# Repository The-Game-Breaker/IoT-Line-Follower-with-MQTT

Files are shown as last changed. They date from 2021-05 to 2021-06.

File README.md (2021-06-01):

# IoT Project
# Hardware
## Gebruikte hardware
### Electronica
| Item | Discription | Price | Qty | Extra costs | Total |
| --- | --- | --- | --- | --- | --- |
| Cytron Maker Line | Simplifying Line Sensor for BeginnersSKU: 19064  |  11,95 € | 1 | |  11,95 €  |
| Shipping Sensor | Shipping elektor | | 1 |  7,95 € |  7,95 € |
| PCB mainboard | PCB robot driver board |  0,51 €  | 1 | |  0,51 € |
| SHIPPING CHARGE | SHIPPING | | 1 |  12,63 € |  12,63 €  |
| PAYPAL FEE | PAYPAL FEE | | 1 |  0,41 € |  0,41 € |
| DRV8825 driver | DSD00010 \_Stepstick DRV8825 drive with heatsink |  5,00 €  | 2 | |  10,00 €  |
| Inbusstelschroef M4x5 | DBM00194 \_Inbusstelschroef M4x5 (10 stuks) |  2,30 €  | 1 | |  2,30 € |
| Verzend- en administratiekosten | Verzend- en administratiekosten 123-3D.nl | | 1 |  5,95 € |  5,95 € |
| Lipo Battery | Yuki Kryptonium 3S 11.1V 30C 5000mAh LiPo 801323 |  45,99 € | 1 | |  45,99 €  |
| Step-Down Buck Converter | DEBO DCDC DOWN 4 (mini 360) |  2,02 €  | 1 | |  2,02 € |
| Dupont kit | Dupont connector kit |  5,00 €  | 1 | |  5,00 € |
| Fuse holder | fuse holder |  0,30 €  | 1 | |  0,30 € |
| Fuse | fuse 2A |  0,20 €  | 1 | |  0,20 € |
| RGB led | RGB common cathode |  1,03 €  | 2 | |  2,06 € |
| 3mm led | 3mm led red |  0,05 €  | 2 | |  0,10 € |
| Resistors | resistors various values |  0,02 €  | 8 | |  0,13 € |
| HC-SR04 | HC-SR04 Ultrasonic sensor – afstandsmeter |  3,00 €  | 1 | |  3,00 € |
| capacator | capacator |  0,11 €  | 2 | |  0,22 € |
| 3D print | 3d prints materiaal+manafacturing |  20,00 € | 1 | |  20,00 €  |
| Lasercut frame | laserkcut frame matriaal+manafacturing |  20,00 € | 1 | |  20,00 €  |
| Stepper motor | JK42HS34-1334 |  13,00 € | 2 | |  26,00 €  |
| Hardware | varous nuts and bolts |  15,00 € | 1 | |  15,00 €  |
| Knikkers | knikkers |  0,20 €  | 2 | |  0,40 € |
| | | | | |  192,12 € |
#### Cytron Maker-Line

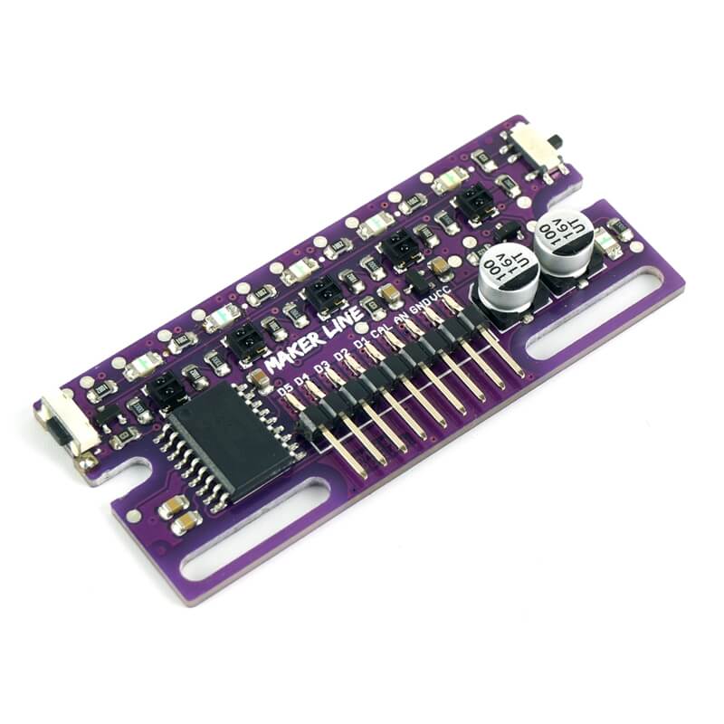
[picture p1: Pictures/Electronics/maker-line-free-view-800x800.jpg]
maker-line-free-view-800x800


De Cytron Maker-Line is een ir sensor array voorzien van 5 sensoren die de lijn uitlezen. Op basis van deze output sturen we de motoren aan. Deze module geeft ook nog wat extra &quot;creature-comforts&quot;, zo is de array gemakkelijk te kalibreren en kan deze &quot;geswitchted&quot; worden tussen een donkere of lichte lijn.

#### HC-SR04

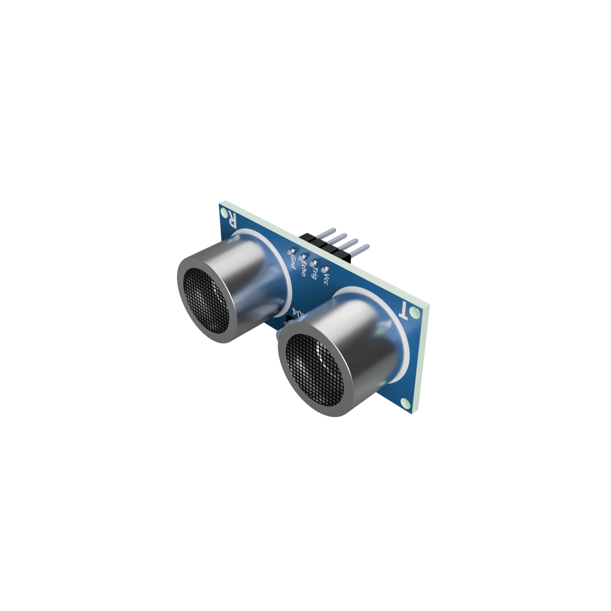
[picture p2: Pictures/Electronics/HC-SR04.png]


De HC-SR04 is een ultrasone sensor. Deze moet ervoor zorgen dat het wagentje nergens tegenaan rijdt. Dit wordt tot stand gebracht met ultrasone echolocatie.

#### Joy-IT Esp32
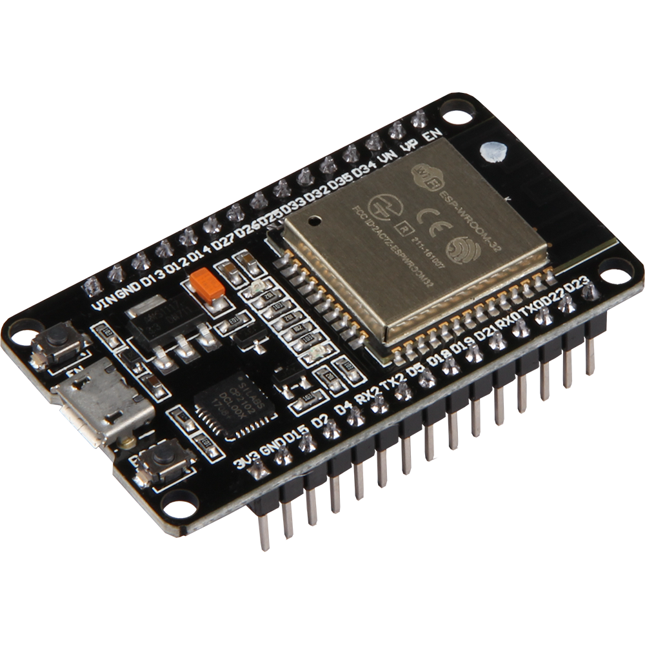
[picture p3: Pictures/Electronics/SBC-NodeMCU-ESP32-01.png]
 

Het brein van het project wordt de ESP32 van JOY-IT. Deze zal alle in- en outputs aansturen en data communiceren via wifi.

### nema17 stepper motor

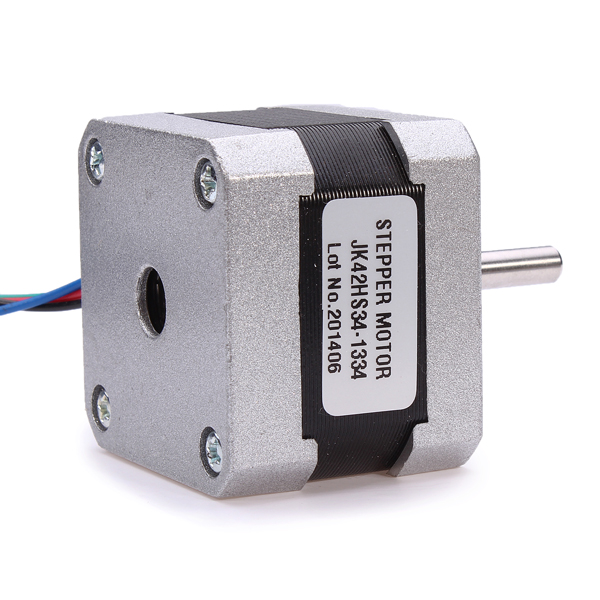
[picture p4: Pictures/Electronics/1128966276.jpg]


Deze JK42HS34-1334 NEMA 17 stepper motoren worden gebruikt om het wagentje aan te drijven. Hoewel niet de ideale keuze, bieden ze toch enige flexibiliteit ten opzichte van andere oplossingen. Een andere factor voor deze keuze was dat ik deze nog had liggen en ik er graag eens mee wilde werken.

#### DRV8825 stepper motor driver

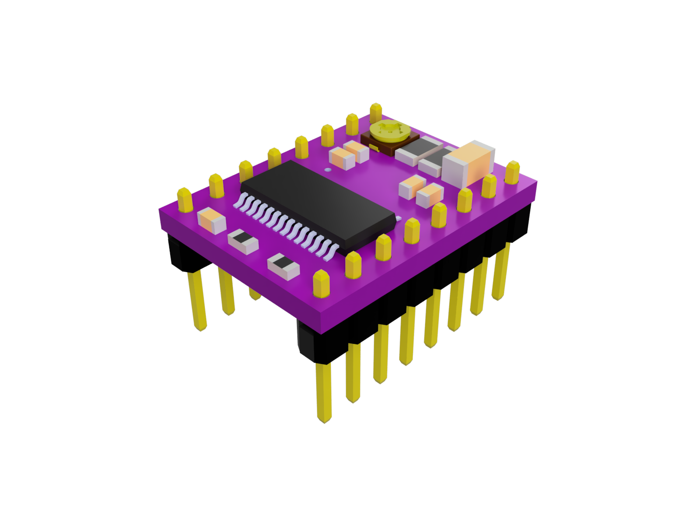
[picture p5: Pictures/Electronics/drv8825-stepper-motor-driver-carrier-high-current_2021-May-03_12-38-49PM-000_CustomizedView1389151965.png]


De DRV8825 wordt gebruikt om de NEMA 17 motoren aan te sturen. Niet alleen biedt deze driver een hogere ampère levering, de microsteps kunnen ook makkelijk worden ingesteld

#### RGB LED 5mm

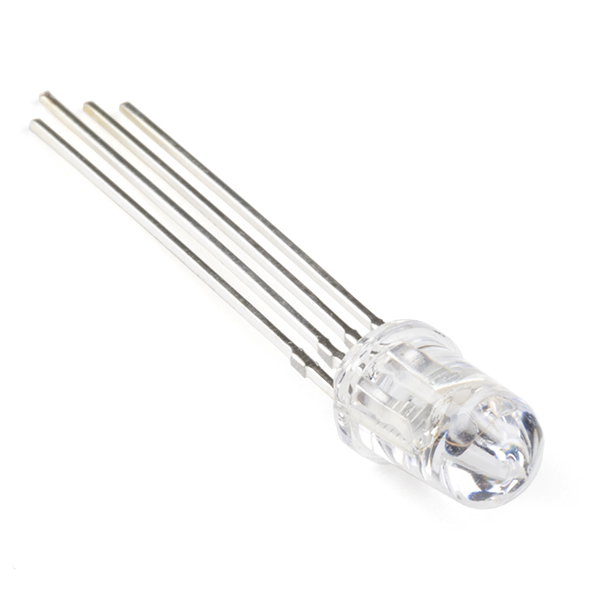
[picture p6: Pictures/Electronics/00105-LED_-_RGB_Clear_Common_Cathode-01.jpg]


Deze led wordt gebruikt als indicator voor de status van het wagentje.

Deze statussen zijn:

- Rood: Het wagentje is de lijn kwijt
- Groen: Het wagentje volgt de lijn en geeft aan naar welke kant er wordt gedraaid
- Blauw: Het wagentje stopt voor een obstakel. Dit kan een blokkade of een dwarslijn zijn.

### Schema, PCB
####

Het onderstaand schema geeft de beschreven componenten systematisch weer.

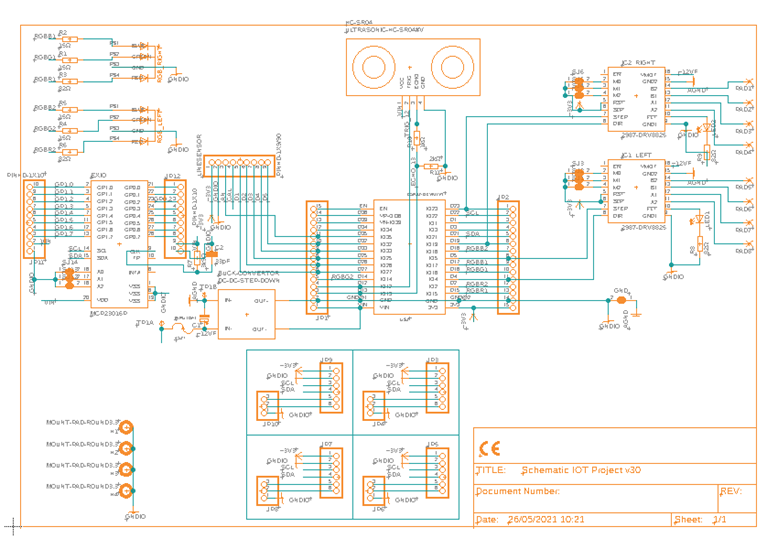
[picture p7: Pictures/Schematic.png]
 
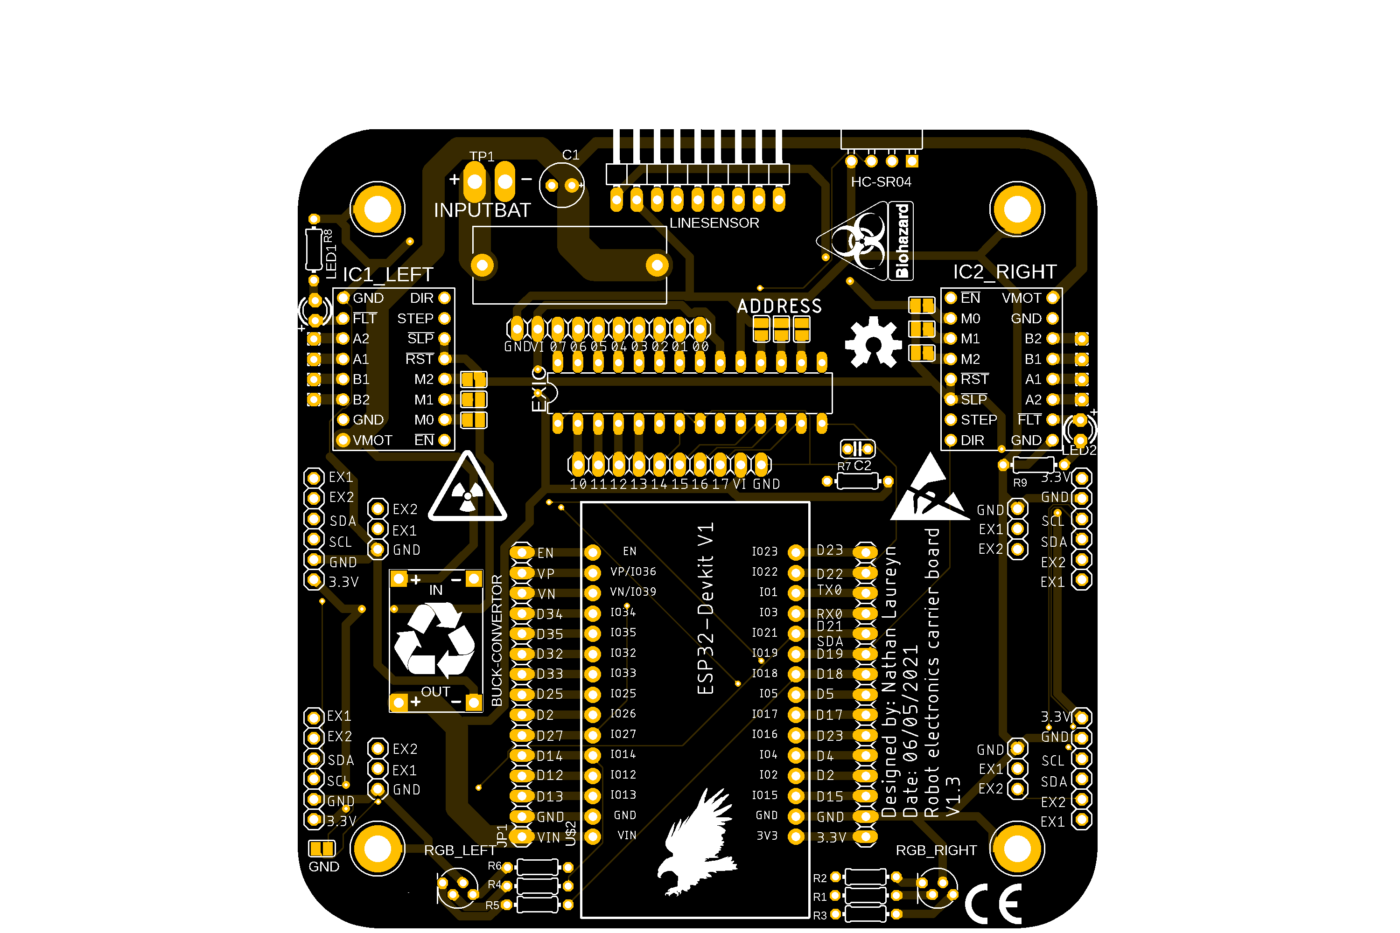
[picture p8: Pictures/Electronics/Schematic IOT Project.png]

### Hardware, andere componenten
#### Chassis



Het chassis bestaat uit een eigen ontwerp vervaardigd uit plexiglas en 3D-geprinte (r)PETG-onderdelen. Deze zijn aan elkaar verbonden met M3, M4 en M5 bouten en moeren uit RVS.
#### Wielen

Er zijn 2 wielen voorzien die instaan voor de aandrijving en sturing van het wagentje. Deze komen oorspronkelijk van een RC-auto. Ook zijn er 2 kogelwieltjes voorzien om het wagentje stabiel te houden.
# Code
## Overview
Programmatie werd geschreven in Visual Studio Code met platformio. Dit geeft een aantal voordelen qua debuggen en foutcontrole maar brengt ook een aantal challenges met zich mee. De code wordt opgedeeld in verschillende onderdelen.

### Setup: includes, definities, integers, etc.

Eerst vinden we een sectie met declaraties en setup voor de verschillende onderdelen van het wagentje. Ook vinden we enkele &quot;macro&#39;s&quot;; deze worden gebruikt om de code en functies later leesbaarder te houden.

### Functies
Vervolgens vinden we een sectie waarin de functies zijn geschreven. Deze worden later opgevraagd door de verschillende taken of andere functies.

### Taken

Onder de functies vinden we een sectie met &quot;Tasks&quot;. Hier worden de functies gedeclareerd die later door de ESP&#39;s FreeRTOS zullen worden opgevraagd.

### Setup en Loop

Tot slot vinden we de sectie setup, hier worden de pinnen gedeclareerd en geïnitialiseerd, ook de taken worden hier toegevoegd. De loop-functie wordt in praktijk niet gebruikt in dit geval.

## FreeRTOS

In de programmatie ben ik voor een systeem gegaan met FreeRTOS in plaats van een meer traditioneel systeem. Ik heb hiervoor gekozen omdat dit het gemakkelijk en efficiënt maakt om te multitasken. Het zorgt er ook voor dat in de toekomst uitbreidingen makkelijk mogelijk zijn.

FreeRTOS werkt een beetje als een scheduler, enkel is deze ingebouwd in de ESP en vraagt dus geen extra libraries. Tevens biedt de RTOS ook een uitgebreid pakket aan opties. Zo kan je bijvoorbeeld een bepaalde taak aan een bepaalde &quot;core&quot; toewijzen en zo &quot;echte&quot; synchrone taken uitvoeren.

## Case system

| Case nr. | Sensors | L | ML | M | MR | R | Dist |
| --- | --- | --- | --- | --- | --- | --- | --- |
| 1 | ExtremeLeft | ON | OFF | OFF | OFF | OFF | OFF |
| 2 | HardLeft | ON | ON | OFF | OFF | OFF | OFF |
| 3 | MediumLeft | OFF | ON | OFF | OFF | OFF | OFF |
| 4 | SoftLeft | OFF | ON | ON | OFF | OFF | OFF |
| 5 | Strait | OFF | OFF | ON | OFF | OFF | OFF |
| 6 | SoftRight | OFF | OFF | ON | ON | OFF | OFF |
| 7 | MediumRight | OFF | OFF | OFF | ON | OFF | OFF |
| 8 | HardRight | OFF | OFF | OFF | ON | ON | OFF |
| 9 | ExtremeRight | OFF | OFF | OFF | OFF | ON | OFF |
| 10 | CrossLine | ON | ON | ON | ON | ON | OFF |
| 11 | LOSTLine | OFF | OFF | OFF | OFF | OFF | OFF |
| 12 | Objectdetect | OFF | OFF | OFF | OFF | OFF | ON |

In de programmatie test de microcontroller de sensorwaarde voor verschillende cases. Aan de hand van deze waarde wordt er een &quot;casenummer&quot; gegeven. Deze kan dan worden opgevraagd door een andere taak, in dit geval de motor sturing taak (taskstep).
![](RackMultipart20210601-4-1wbuym5_html_b8db10d83fbda782.png
## Wifi en MQTT

De ESP is voorzien van een &quot;library&quot; waarmee hij via wifi met een mqtt server kan verbinden. Deze kan zowel &quot;subscriben&quot; als &quot;publishen&quot;. Zo kan hij communiceren met de node red server.
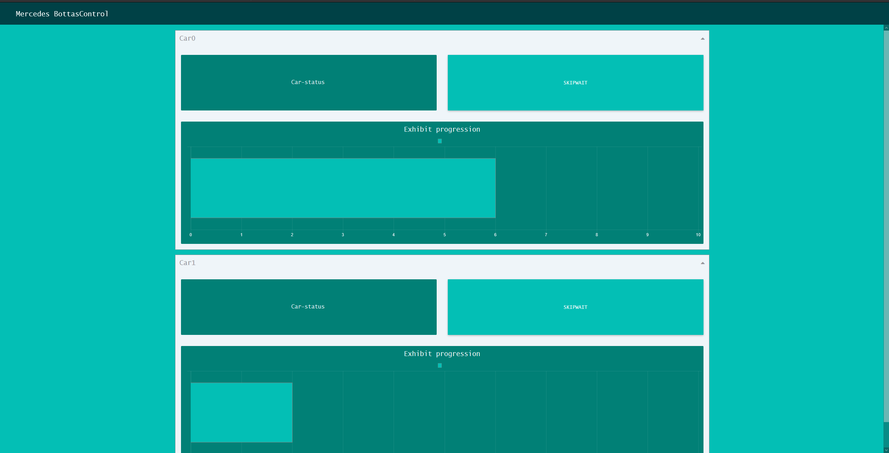
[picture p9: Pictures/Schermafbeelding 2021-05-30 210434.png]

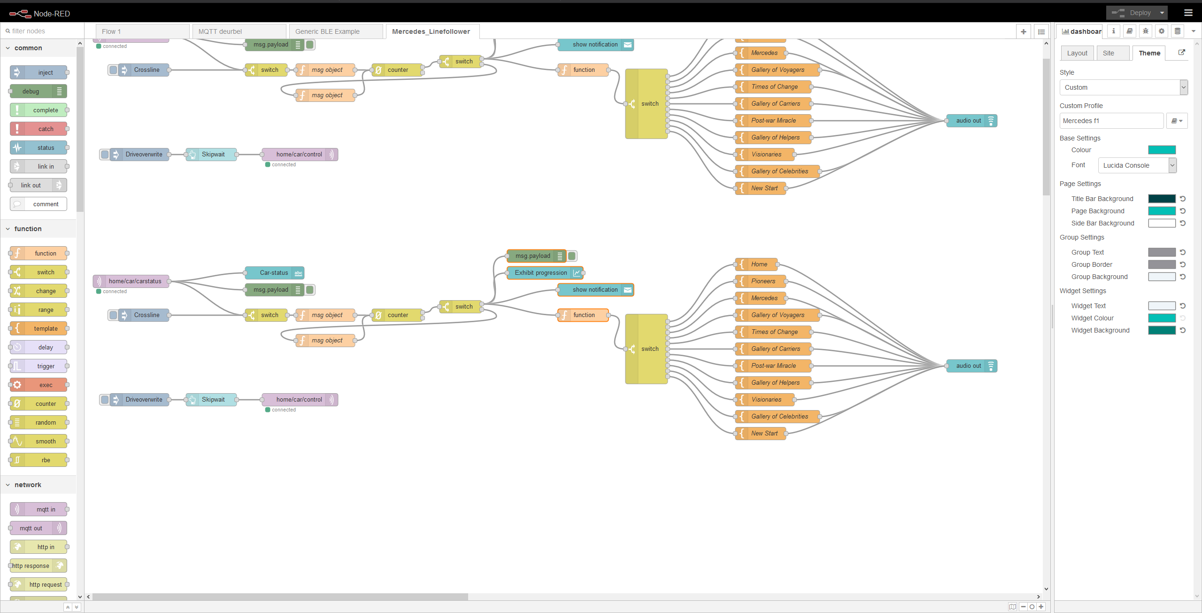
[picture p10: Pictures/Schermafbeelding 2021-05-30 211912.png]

# Tutorial

## Prerequisites

Tijdens de tutorial wordt ervan uitgegaan dat er kennis is van volgende elementen:

- Elektronica
- Mechanica
- ESP32 en software
- MQTT
- Node Red
- Netwerken

## Stap 1: Acquiring hardware

De eerste stap om het wagentje te bouwen is natuurlijk alle hardware en elektronica aan te kopen. Deze onderdelen werden eerder in dit document beschreven onder het deel hardware en zijn ook terug te vinden in de BOM.

## Stap 2: Assemblage

Nadat alle onderdelen zijn aangekomen, kunnen we beginnen met de assemblage van de wagentjes.

### Bodem frame

Bevestig de motor houders, zwenkwieltjes en batterijhouder aan het bodem frame met de bijhorende bouten, moeren en rondellen.

### Midden frame

Bevestig de stapper motoren in de motorhouders. Installeer de &quot;support poles&quot; op de bodemplaat. Installeer ook de bumper met line sensor.

### Boven frame

Installeer het boven frame op de &quot;support poles&quot; en bevestig deze. Installeer vervolgens de mounting bracket voor de afstandssenor.

### PCB

Soldeer alle componenten op de PCB behalve de motorkabels.

### Elektronica bevestigen

Bevestig de servo op het mounting bracket. Neem de afstand sensor en installeer deze op het bovendeel van het mounting bracket en installeer het geheel vervolgens op de servomotor. Bevestig vervolgens de pcb met de bijhorende bouten, moeren en &quot;standoffs&quot; op het boven frame.

### Afmontage Elektronica

Tot slot worden alle kabels getrokken en verbonden met de bijhorende onderdelen volgens onderstaand schema.



## Stap 3: MQTT and node red

Installeer een MQTT en Node Red server. Hierbij kan gebruik gemaakt worden van een raspberry pi.

Installeer de node-red flow voor de wagensturing.

## Stap 4: Programmatie ESP32

Nu we een MQTT-server hebben, moeten we de ESP32 programmeren. Vergeet niet voor het programmeren de code aan te passen aan de huidige situatie (wifi ssid, password, etc.). Programmeer vervolgens ESP.

## Stap 5 Aanleggen van het parcours

Het aanleggen van het parcours kan simpelweg worden gedaan door het trekken van een zwarte lijn op lichte grond of witte lijn op donkere grond. Vervolgens kunnen er dwarslijnen voorzien worden om het wagentje te stoppen op de &quot;points of intrest&quot;.

## Stap 6 Tewerkstelling

Tot slot kunnen de wagentjes in werking worden gesteld. Door deze op de lijn te plaatsen en de batterij in te steken.

# Resources

[https://grabcad.com/library/esp-wroom-32-2](https://grabcad.com/library/esp-wroom-32-2)

[https://www.cytron.io/p-maker-line-simplifying-line-sensor-for-beginner](https://www.cytron.io/p-maker-line-simplifying-line-sensor-for-beginner)

[https://www.jkongmotor.com/product/42HS-NEMA17-2Phase-Stepper-Motor-1-8%C2%B0.html](https://www.jkongmotor.com/product/42HS-NEMA17-2Phase-Stepper-Motor-1-8%C2%B0.html)

[https://www.thingiverse.com/thing:4275668/files](https://www.thingiverse.com/thing:4275668/files)

[https://www.makerguides.com/wp-content/uploads/2019/02/DRV8825-Arduino-stepper-motor-wiring-schematic-diagram-pinout\_bb-1024x551.jpg](https://www.makerguides.com/wp-content/uploads/2019/02/DRV8825-Arduino-stepper-motor-wiring-schematic-diagram-pinout_bb-1024x551.jpg)

[https://www.makerguides.com/drv8825-stepper-motor-driver-arduino-tutorial/](https://www.makerguides.com/drv8825-stepper-motor-driver-arduino-tutorial/)

[https://github.com/suzakulab/Eagle-Library-Pololu](https://github.com/suzakulab/Eagle-Library-Pololu)

[https://www.diymodules.org/eagle-show-object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](https://www.diymodules.org/eagle-show-object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)

[https://www.airspayce.com/mikem/arduino/AccelStepper/index.html](https://www.airspayce.com/mikem/arduino/AccelStepper/index.html)

[https://www.microchip.com/wwwproducts/en/MCP23016](https://www.microchip.com/wwwproducts/en/MCP23016)

[https://www.instructables.com/IO-Expander-for-ESP32-ESP8266-and-Arduino/](https://www.instructables.com/IO-Expander-for-ESP32-ESP8266-and-Arduino/)

[https://github.com/arkhipenko/TaskScheduler](https://github.com/arkhipenko/TaskScheduler)

[https://ozh.github.io/ascii-tables/](https://ozh.github.io/ascii-tables/)

[https://www.studiopieters.nl/esp32-pinout/](https://www.studiopieters.nl/esp32-pinout/)

[https://flows.nodered.org/node/node-red-dashboard](https://flows.nodered.org/node/node-red-dashboard)

## Colors:

 #004146 RGB (0,65,70)
 
 #018076 RGB (1,128,118)
 
 #03BFB5 RGB (3,191,181)
 
 #949398 RGB (148,147,152)
 
 #EFF5F9 RGB (239,245,249)

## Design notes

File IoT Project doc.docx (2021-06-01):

1/06/2021

Nathan Laureyn

# IoT Project

# Artikel I. Hardware

## Sectie I.1 Gebruikte hardware

### (a) Electronica

#### (i) Cytron Maker-Line


De Cytron Maker-Line is een ir sensor array voorzien van 5 sensoren die de lijn uitlezen. Op basis van deze output sturen we de motoren aan. Deze module geeft ook nog wat extra “creature-comforts”, zo is de array gemakkelijk te kalibreren en kan deze “geswitchted” worden tussen een donkere of lichte lijn.

#### (ii) HC-SR04

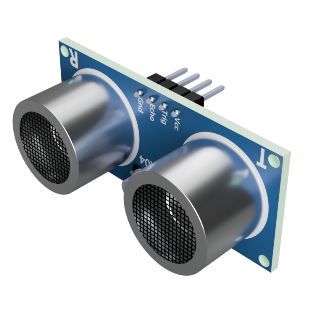
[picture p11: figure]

De HC-SR04 is een ultrasone sensor. Deze moet ervoor zorgen dat het wagentje nergens tegenaan rijdt. Dit wordt tot stand gebracht met ultrasone echolocatie.

#### (iii) Joy-IT Esp32

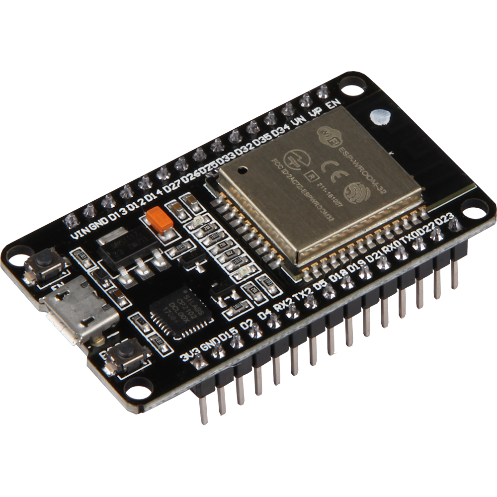
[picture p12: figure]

Het brein van het project wordt de ESP32 van JOY-IT. Deze zal alle in- en outputs aansturen en data communiceren via wifi.

### (b) nema17 stepper motor

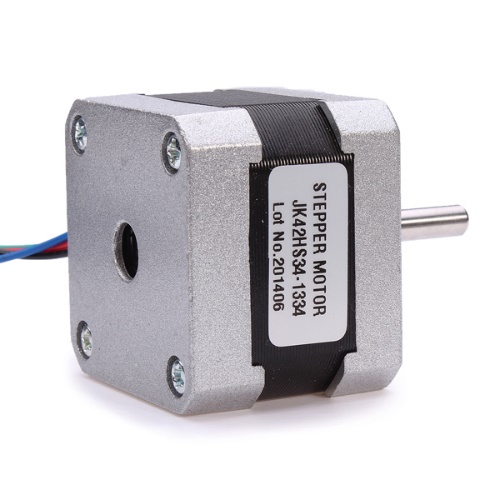
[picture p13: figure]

Deze JK42HS34-1334 NEMA 17 stepper motoren worden gebruikt om het wagentje aan te drijven. Hoewel niet de ideale keuze, bieden ze toch enige flexibiliteit ten opzichte van andere oplossingen. Een andere factor voor deze keuze was dat ik deze nog had liggen en ik er graag eens mee wilde werken.

#### (i) DRV8825 stepper motor driver

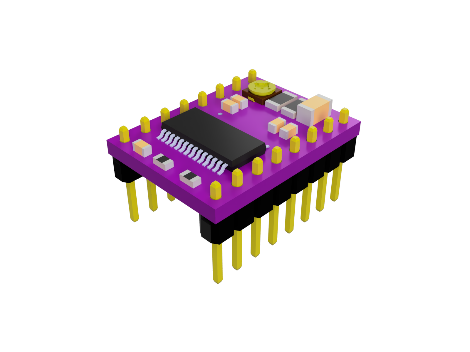
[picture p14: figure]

De DRV8825 wordt gebruikt om de NEMA 17 motoren aan te sturen. Niet alleen biedt deze driver een hogere ampère levering, de microsteps kunnen ook makkelijk worden ingesteld

#### (iii) RGB LED 5mm

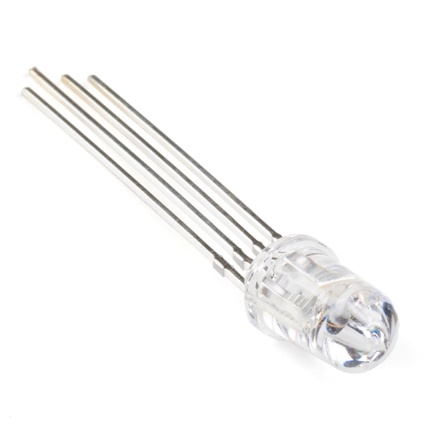
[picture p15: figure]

Deze led wordt gebruikt als indicator voor de status van het wagentje.

Deze statussen zijn:

- Rood: Het wagentje is de lijn kwijt
- Groen: Het wagentje volgt de lijn en geeft aan naar welke kant er wordt gedraaid
- Blauw: Het wagentje stopt voor een obstakel. Dit kan een blokkade of een dwarslijn zijn.

### (c) Schema, PCB

Het onderstaand schema geeft de beschreven componenten systematisch weer.

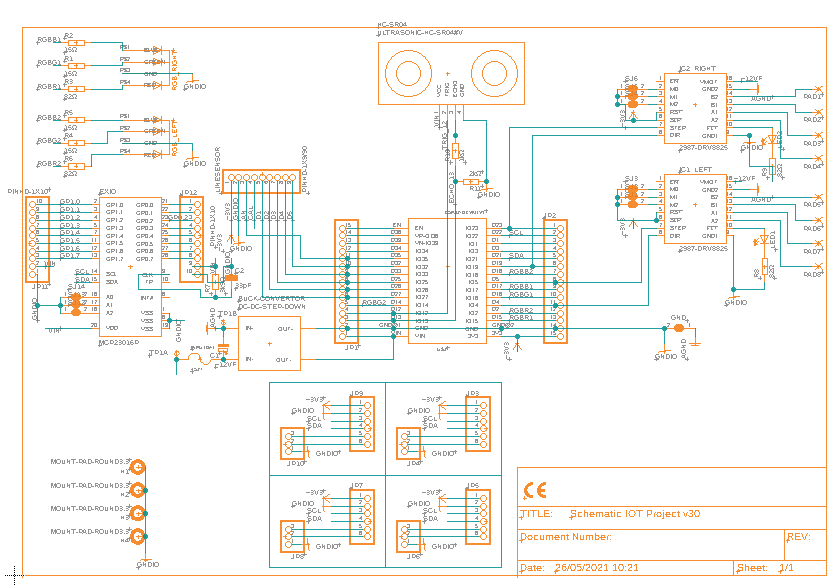
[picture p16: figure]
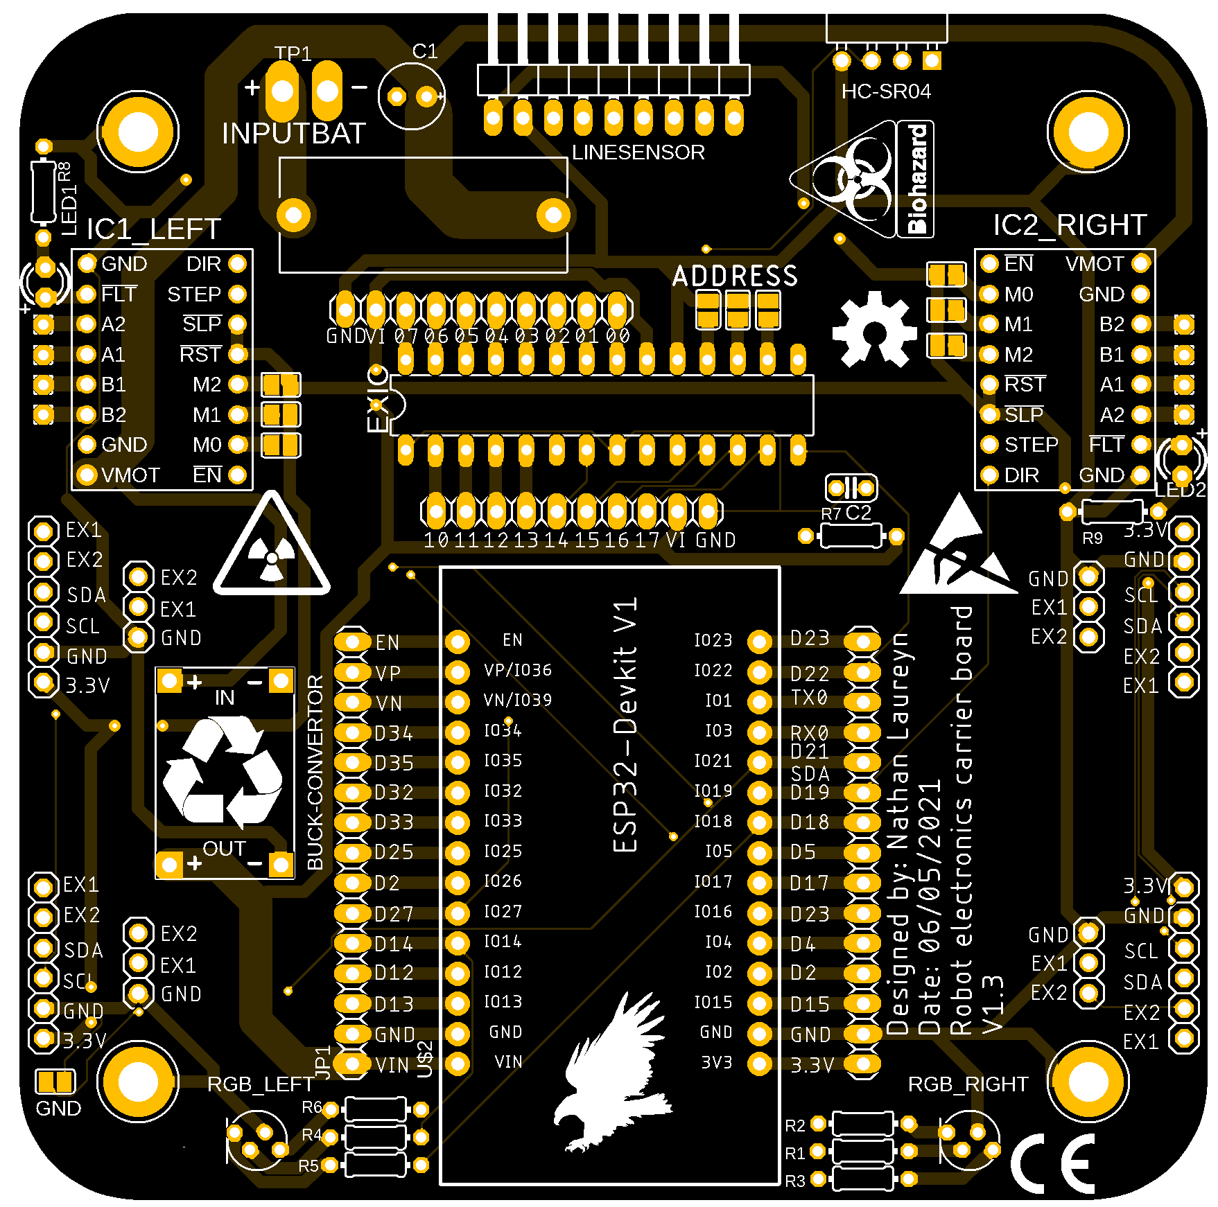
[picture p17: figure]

### (d) Hardware, andere componenten

#### (i) Chassis

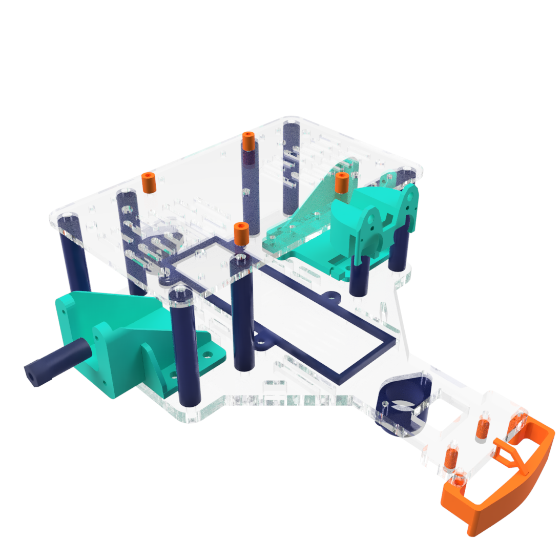
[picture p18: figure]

Het chassis bestaat uit een eigen ontwerp vervaardigd uit plexiglas en 3D-geprinte (r)PETG-onderdelen. Deze zijn aan elkaar verbonden met M3, M4 en M5 bouten en moeren uit RVS.

#### (ii) Wielen

Er zijn 2 wielen voorzien die instaan voor de aandrijving en sturing van het wagentje. Deze komen oorspronkelijk van een RC-auto. Ook zijn er 2 kogelwieltjes voorzien om het wagentje stabiel te houden.

# Artikel II. Code

## Sectie II.1 Overview

Programmatie werd geschreven in Visual Studio Code met platformio. Dit geeft een aantal voordelen qua debuggen en foutcontrole maar brengt ook een aantal challenges met zich mee. De code wordt opgedeeld in verschillende onderdelen.

### (a) Setup: includes, definities, integers, etc.

Eerst vinden we een sectie met declaraties en setup voor de verschillende onderdelen van het wagentje. Ook vinden we enkele “macro’s”; deze worden gebruikt om de code en functies later leesbaarder te houden.

### (b) Functies

Vervolgens vinden we een sectie waarin de functies zijn geschreven. Deze worden later opgevraagd door de verschillende taken of andere functies.

### (c) Taken

Onder de functies vinden we een sectie met “Tasks”. Hier worden de functies gedeclareerd die later door de ESP’s FreeRTOS zullen worden opgevraagd.

### (d) Setup en Loop

Tot slot vinden we de sectie setup, hier worden de pinnen gedeclareerd en geïnitialiseerd, ook de taken worden hier toegevoegd. De loop-functie wordt in praktijk niet gebruikt in dit geval.

## Sectie II.2 FreeRTOS

In de programmatie ben ik voor een systeem gegaan met FreeRTOS in plaats van een meer traditioneel systeem. Ik heb hiervoor gekozen omdat dit het gemakkelijk en efficiënt maakt om te multitasken. Het zorgt er ook voor dat in de toekomst uitbreidingen makkelijk mogelijk zijn.

FreeRTOS werkt een beetje als een scheduler, enkel is deze ingebouwd in de ESP en vraagt dus geen extra libraries. Tevens biedt de RTOS ook een uitgebreid pakket aan opties. Zo kan je bijvoorbeeld een bepaalde taak aan een bepaalde “core” toewijzen en zo “echte” synchrone taken uitvoeren.

## Sectie II.3 Case system

Case nr. | Sensors | L | ML | M | MR | R | Dist
1 | ExtremeLeft | ON | OFF | OFF | OFF | OFF | OFF
2 | HardLeft | ON | ON | OFF | OFF | OFF | OFF
3 | MediumLeft | OFF | ON | OFF | OFF | OFF | OFF
4 | SoftLeft | OFF | ON | ON | OFF | OFF | OFF
5 | Strait | OFF | OFF | ON | OFF | OFF | OFF
6 | SoftRight | OFF | OFF | ON | ON | OFF | OFF
7 | MediumRight | OFF | OFF | OFF | ON | OFF | OFF
8 | HardRight | OFF | OFF | OFF | ON | ON | OFF
9 | ExtremeRight | OFF | OFF | OFF | OFF | ON | OFF
10 | CrossLine | ON | ON | ON | ON | ON | OFF
11 | LOSTLine | OFF | OFF | OFF | OFF | OFF | OFF
12 | Objectdetect | OFF | OFF | OFF | OFF | OFF | ON

In de programmatie test de microcontroller de sensorwaarde voor verschillende cases. Aan de hand van deze waarde wordt er een “casenummer” gegeven. Deze kan dan worden opgevraagd door een andere taak, in dit geval de motor sturing taak (taskstep).

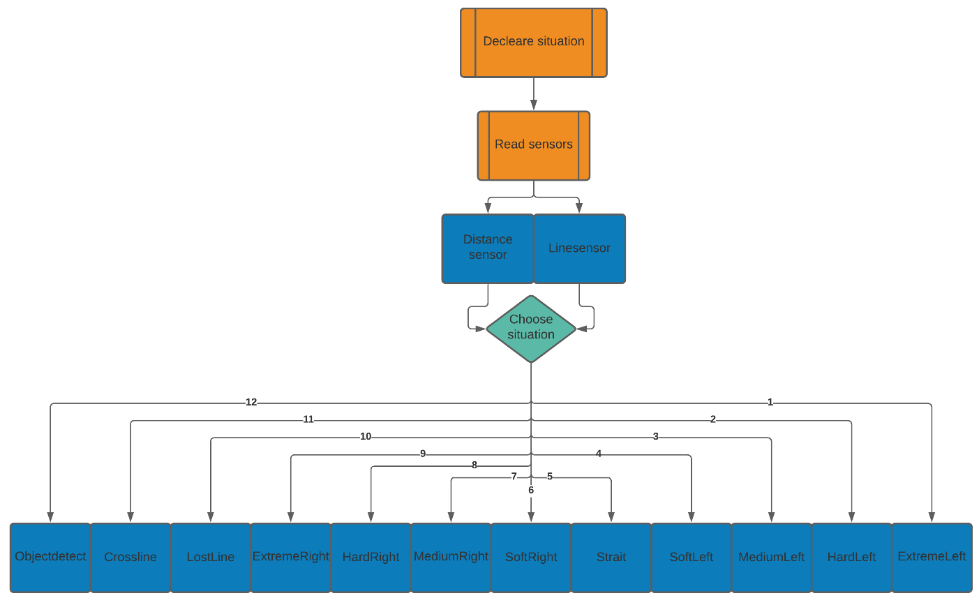
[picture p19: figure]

## Sectie II.4 Wifi en MQTT

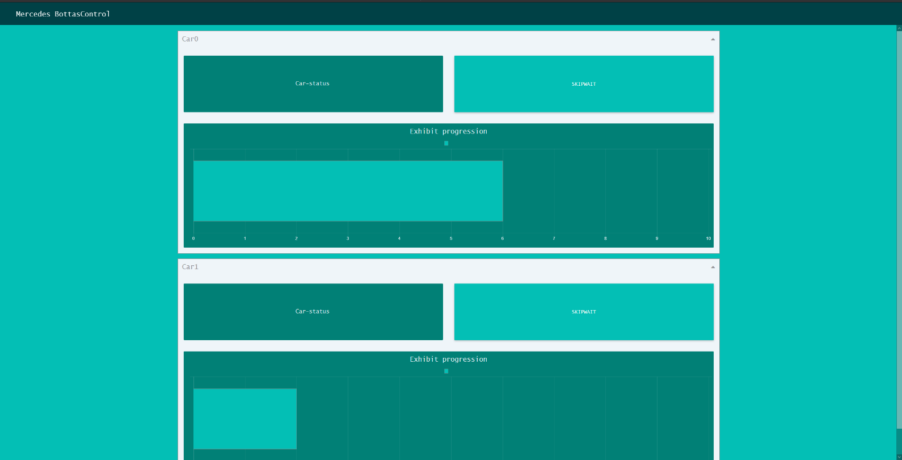
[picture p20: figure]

De ESP is voorzien van een “library” waarmee hij via wifi met een mqtt server kan verbinden. Deze kan zowel “subscriben” als “publishen”. Zo kan hij communiceren met de node red server.

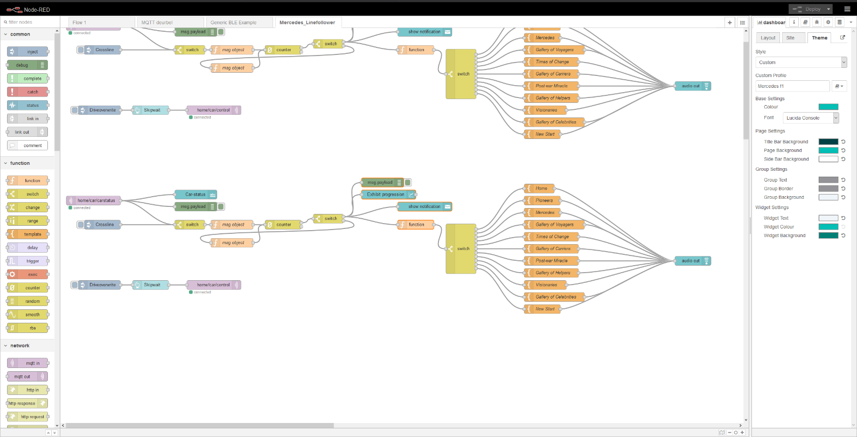
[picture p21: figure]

# Artikel III. Tutorial

## Sectie III.1 Prerequisites

Tijdens de tutorial wordt ervan uitgegaan dat er kennis is van volgende elementen:

- Elektronica
- Mechanica
- ESP32 en software
- MQTT
- Node Red
- Netwerken

## Sectie III.2 Stap 1: Acquiring hardware

De eerste stap om het wagentje te bouwen is natuurlijk alle hardware en elektronica aan te kopen. Deze onderdelen werden eerder in dit document beschreven onder het deel hardware en zijn ook terug te vinden in de BOM.

## Sectie III.3 Stap 2: Assemblage

Nadat alle onderdelen zijn aangekomen, kunnen we beginnen met de assemblage van de wagentjes.

### (a) Bodem frame

Bevestig de motor houders, zwenkwieltjes en batterijhouder aan het bodem frame met de bijhorende bouten, moeren en rondellen.

### (b) Midden frame

Bevestig de stapper motoren in de motorhouders. Installeer de “support poles” op de bodemplaat. Installeer ook de bumper met line sensor.

### (c) Boven frame

Installeer het boven frame op de “support poles” en bevestig deze. Installeer vervolgens de mounting bracket voor de afstandssenor.

### (d) PCB

Soldeer alle componenten op de PCB behalve de motorkabels.

### (e) Elektronica bevestigen

Bevestig de servo op het mounting bracket. Neem de afstand sensor en installeer deze op het bovendeel van het mounting bracket en installeer het geheel vervolgens op de servomotor. Bevestig vervolgens de pcb met de bijhorende bouten, moeren en “standoffs” op het boven frame.

### (f) Afmontage Elektronica

Tot slot worden alle kabels getrokken en verbonden met de bijhorende onderdelen volgens onderstaand schema.

## Sectie III.4 Stap 3: MQTT and node red

Installeer een MQTT en Node Red server. Hierbij kan gebruik gemaakt worden van een raspberry pi.

Installeer de node-red flow voor de wagensturing.

## Sectie III.5 Stap 4: Programmatie ESP32

Nu we een MQTT-server hebben, moeten we de ESP32 programmeren. Vergeet niet voor het programmeren de code aan te passen aan de huidige situatie (wifi ssid, password, etc.). Programmeer vervolgens ESP.

## Sectie III.6 Stap 5 Aanleggen van het parcours

Het aanleggen van het parcours kan simpelweg worden gedaan door het trekken van een zwarte lijn op lichte grond of witte lijn op donkere grond. Vervolgens kunnen er dwarslijnen voorzien worden om het wagentje te stoppen op de “points of intrest”.

## Sectie III.7 Stap 6 Tewerkstelling

Tot slot kunnen de wagentjes in werking worden gesteld. Door deze op de lijn te plaatsen en de batterij in te steken.

# Artikel IV. Resources

https://grabcad.com/library/esp-wroom-32-2

https://www.cytron.io/p-maker-line-simplifying-line-sensor-for-beginner

https://www.jkongmotor.com/product/42HS-NEMA17-2Phase-Stepper-Motor-1-8%C2%B0.html

https://www.thingiverse.com/thing:4275668/files

https://www.makerguides.com/wp-content/uploads/2019/02/DRV8825-Arduino-stepper-motor-wiring-schematic-diagram-pinout_bb-1024x551.jpg

https://www.makerguides.com/drv8825-stepper-motor-driver-arduino-tutorial/

https://github.com/suzakulab/Eagle-Library-Pololu

https://www.diymodules.org/eagle-show-object?type=dm&file=diy-modules.lbr&device=DC-DC-STEP-DOWN-MP2307

https://www.airspayce.com/mikem/arduino/AccelStepper/index.html

https://www.microchip.com/wwwproducts/en/MCP23016

https://www.instructables.com/IO-Expander-for-ESP32-ESP8266-and-Arduino/

https://github.com/arkhipenko/TaskScheduler

https://ozh.github.io/ascii-tables/

https://www.studiopieters.nl/esp32-pinout/

https://flows.nodered.org/node/node-red-dashboard

Colors:

#004146 RGB (0,65,70)

#018076 RGB (1,128,118)

#03BFB5 RGB (3,191,181)

#949398 RGB (148,147,152)

#EFF5F9 RGB (239,245,249)

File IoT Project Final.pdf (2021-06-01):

# IoT Project

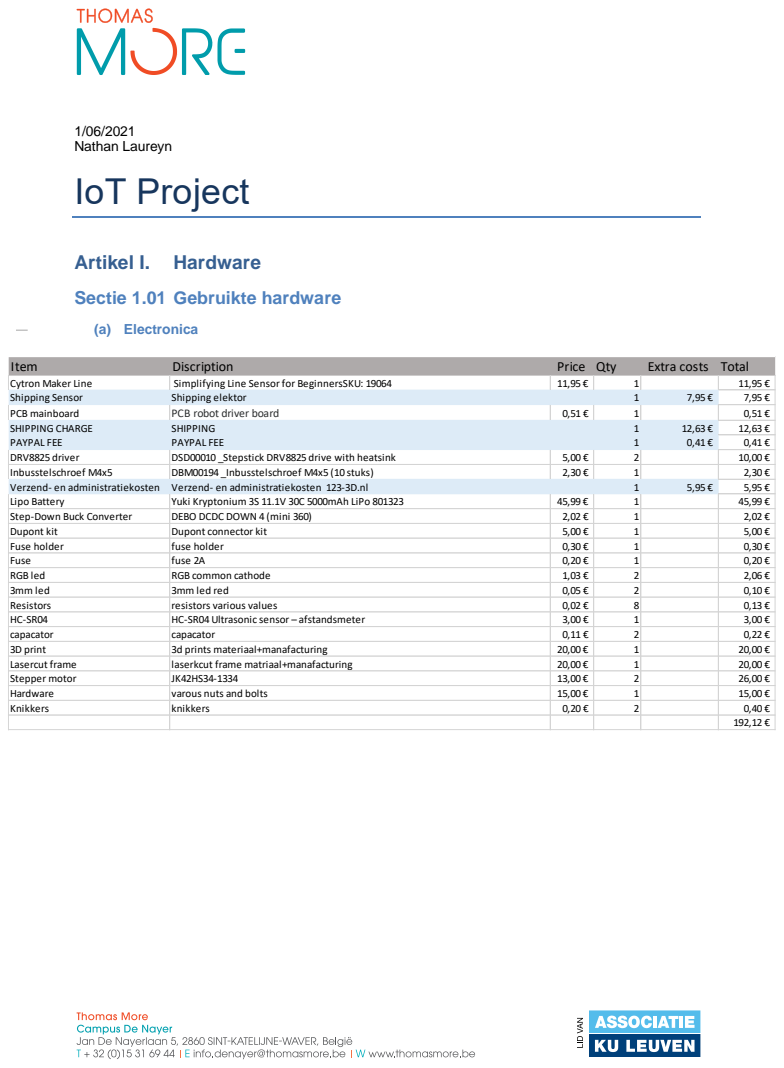
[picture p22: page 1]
1/06/2021 Nathan Laureyn; Artikel I.; Hardware; (a) Electronica; Item; Discription; Price Qty; Extra costs Total; Cytron Maker Line; Simplifying Line Sensor for BeginnersSKU: 19064; Shipping Sensor; Shipping elektor; PCB mainboard; PCB robot driver board; SHIPPING CHARGE; SHIPPING; PAYPAL FEE; DRV8825 driver; DSD00010 _Stepstick DRV8825 drive with heatsink; Inbusstelschroef M4x5; DBM00194 _Inbusstelschroef M4x5 (10 stuks)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

Sectie 1.01 Gebruikte hardware

Step-Down Buck Converter | DEBO DCDC DOWN 4 (mini 360) | 2,02 € | 1 | 2,02 €
Dupont kit | Dupont connector kit | 5,00 € | 1 | 5,00 €
Fuse holder | fuse holder | 0,30 € | 1 | 0,30 €
Fuse | fuse 2A | 0,20 € | 1 | 0,20 €
RGB led | RGB common cathode | 1,03 € | 2 | 2,06 €
3mm led | 3mm led red | 0,05 € | 2 | 0,10 €
Resistors | resistors various values | 0,02 € | 8 | 0,13 €
HC-SR04 | HC-SR04 Ultrasonic sensor – afstandsmeter | 3,00 € | 1 | 3,00 €
capacator | capacator | 0,11 € | 2 | 0,22 €
3D print | 3d prints materiaal+manafacturing | 20,00 € | 1 | 20,00 €
Lasercut frame | laserkcut frame matriaal+manafacturing | 20,00 € | 1 | 20,00 €
Stepper motor | JK42HS34-1334 | 13,00 € | 2 | 26,00 €
Hardware | varous nuts and bolts | 15,00 € | 1 | 15,00 €
Knikkers | knikkers | 0,20 € | 2 | 0,40 €

(i) Cytron Maker-Line

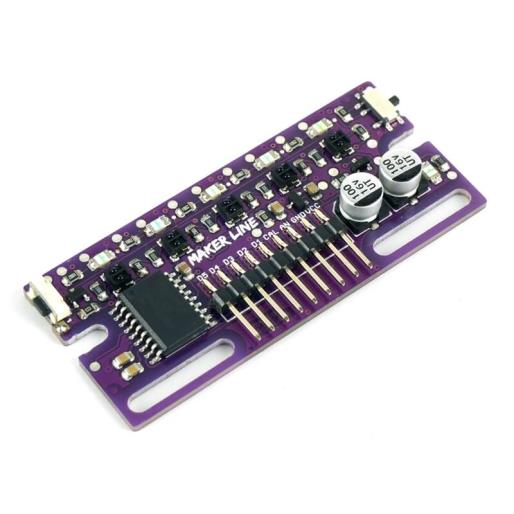
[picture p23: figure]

De Cytron Maker-Line is een ir sensor array voorzien van 5 sensoren die de lijn uitlezen. Op basis van deze output sturen we de motoren aan. Deze module geeft ook nog wat extra “creature-comforts”, zo is de array gemakkelijk te kalibreren en kan deze “geswitchted” worden tussen een donkere of lichte lijn.

(ii) HC-SR04

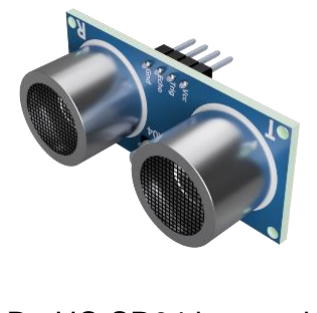
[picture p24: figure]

De HC-SR04 is een ultrasone sensor. Deze moet ervoor zorgen dat het wagentje nergens tegenaan rijdt. Dit wordt tot stand gebracht met ultrasone echolocatie.

(iii) Joy-IT Esp32

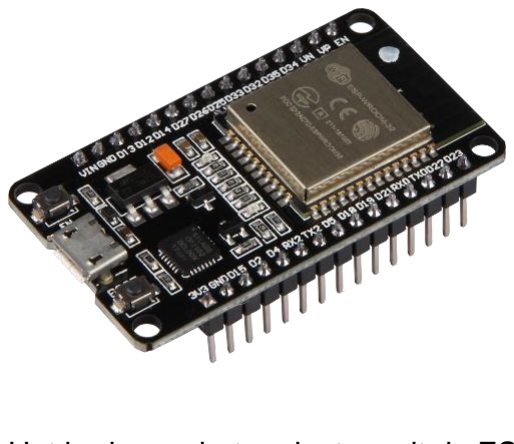
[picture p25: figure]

Het brein van het project wordt de ESP32 van JOY-IT. Deze zal alle in- en outputs aansturen en data communiceren via wifi.

(b) nema17 stepper motor

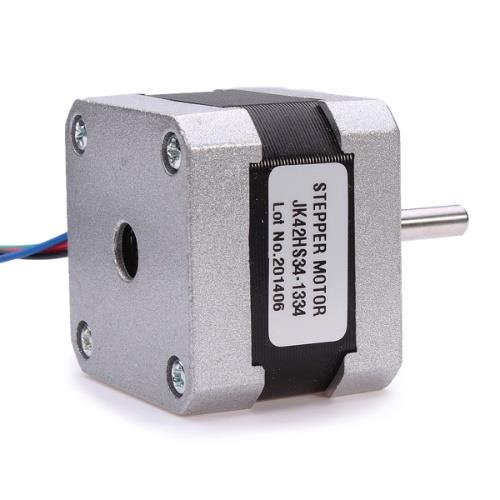
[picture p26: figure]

Deze JK42HS34-1334 NEMA 17 stepper motoren worden gebruikt om het wagentje aan te drijven. Hoewel niet de ideale keuze, bieden ze toch enige flexibiliteit ten opzichte van andere oplossingen. Een andere factor voor deze keuze was dat ik deze nog had liggen en ik er graag eens mee wilde werken.

(i) DRV8825 stepper motor driver

(ii)

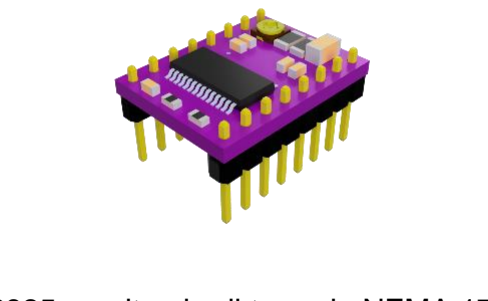
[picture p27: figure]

De DRV8825 wordt gebruikt om de NEMA 17 motoren aan te sturen. Niet alleen biedt deze driver een hogere ampère levering, de microsteps kunnen ook makkelijk worden ingesteld

(iii) RGB LED 5mm

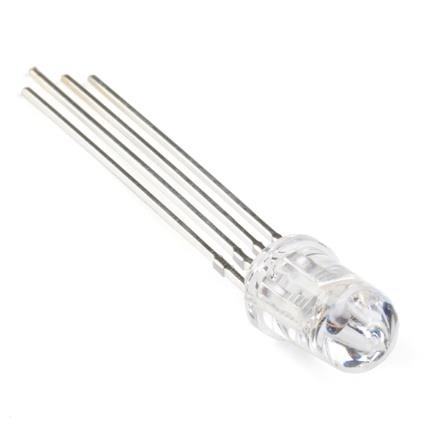
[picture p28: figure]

Deze led wordt gebruikt als indicator voor de status van het wagentje.
Deze statussen zijn:
- Rood: Het wagentje is de lijn kwijt
- Groen: Het wagentje volgt de lijn en geeft aan naar welke kant er wordt gedraaid
- Blauw: Het wagentje stopt voor een obstakel. Dit kan een blokkade of een dwarslijn zijn.

(c) Schema, PCB

(i)
Het onderstaand schema geeft de beschreven componenten systematisch weer.

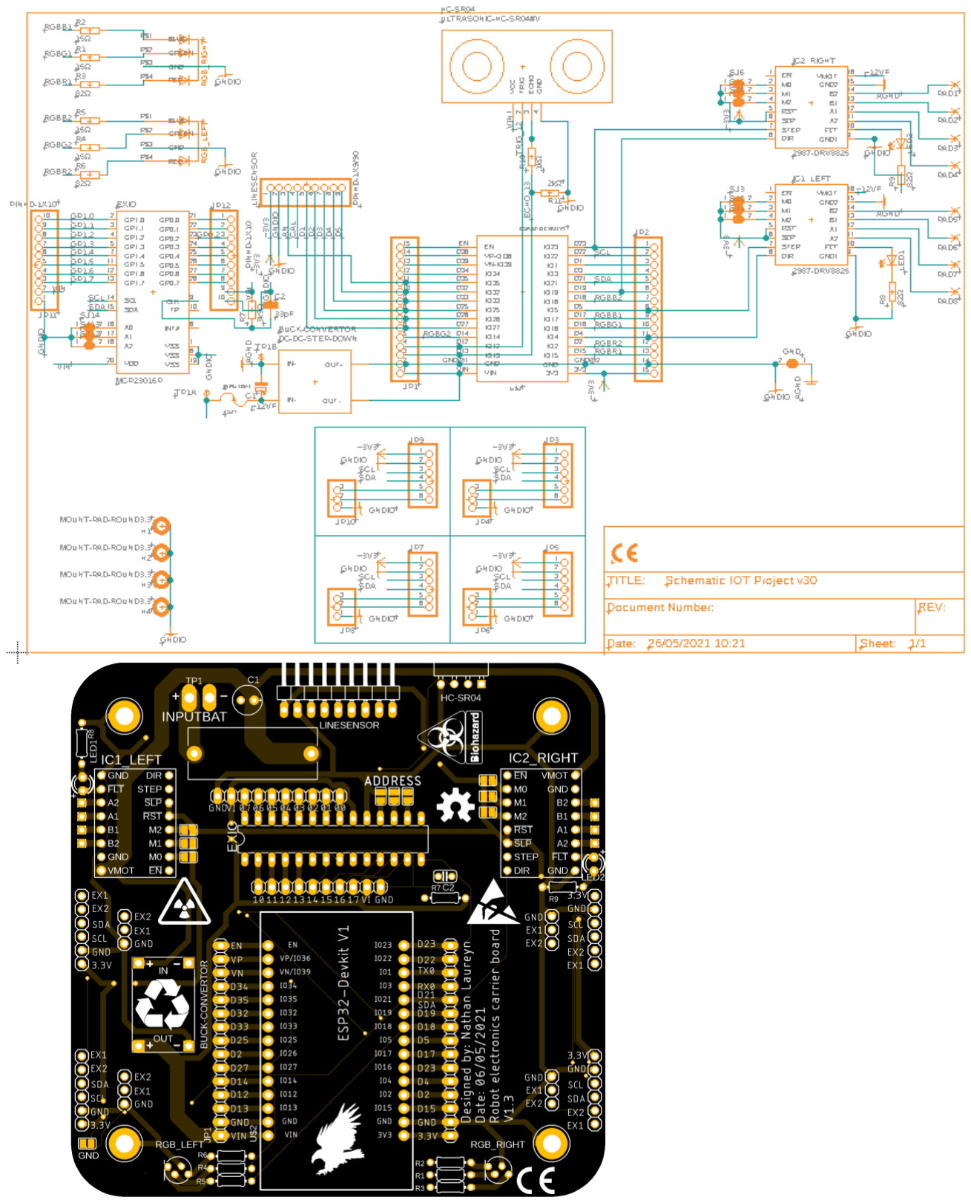
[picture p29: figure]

(d) Hardware, andere componenten
(i) Chassis

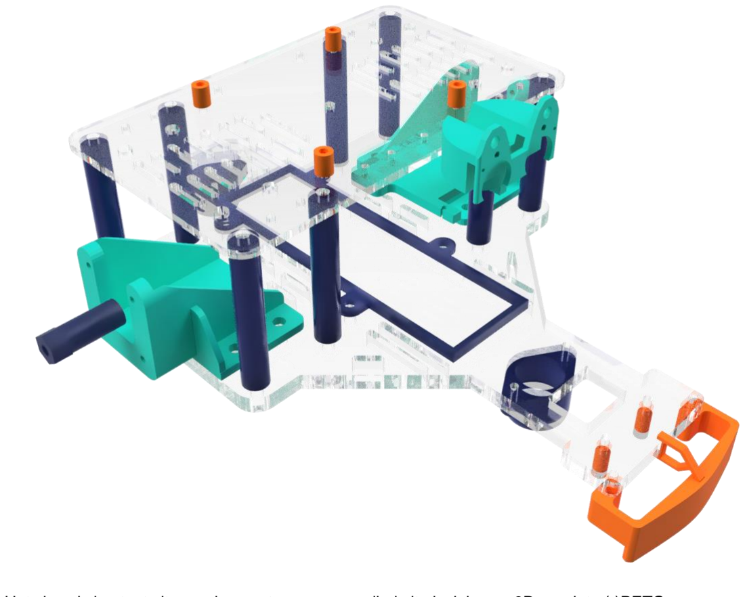
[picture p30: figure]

Het chassis bestaat uit een eigen ontwerp vervaardigd uit plexiglas en 3D-geprinte (r)PETGonderdelen. Deze zijn aan elkaar verbonden met M3, M4 en M5 bouten en moeren uit RVS.

(ii) Wielen
Er zijn 2 wielen voorzien die instaan voor de aandrijving en sturing van het wagentje. Deze komen oorspronkelijk van een RC-auto. Ook zijn er 2 kogelwieltjes voorzien om het wagentje stabiel te houden.

## Artikel II. Code

### Sectie 2.01 Overview

Programmatie werd geschreven in Visual Studio Code met platformio. Dit geeft een aantal voordelen qua debuggen en foutcontrole maar brengt ook een aantal challenges met zich mee. De code wordt opgedeeld in verschillende onderdelen.

(a) Setup: includes, definities, integers, etc.
Eerst vinden we een sectie met declaraties en setup voor de verschillende onderdelen van het wagentje. Ook vinden we enkele “macro’s”; deze worden gebruikt om de code en functies later leesbaarder te houden.
(b) Functies
Vervolgens vinden we een sectie waarin de functies zijn geschreven. Deze worden later opgevraagd door de verschillende taken of andere functies.
(c) Taken
Onder de functies vinden we een sectie met “Tasks”. Hier worden de functies gedeclareerd die later door de ESP’s FreeRTOS zullen worden opgevraagd.
(d) Setup en Loop
Tot slot vinden we de sectie setup, hier worden de pinnen gedeclareerd en geïnitialiseerd, ook de taken worden hier toegevoegd. De loop-functie wordt in praktijk niet gebruikt in dit geval.

### Sectie 2.02 FreeRTOS

In de programmatie ben ik voor een systeem gegaan met FreeRTOS in plaats van een meer traditioneel systeem. Ik heb hiervoor gekozen omdat dit het gemakkelijk en efficiënt maakt om te multitasken. Het zorgt er ook voor dat in de toekomst uitbreidingen makkelijk mogelijk zijn.

FreeRTOS werkt een beetje als een scheduler, enkel is deze ingebouwd in de ESP en vraagt dus geen extra libraries. Tevens biedt de RTOS ook een uitgebreid pakket aan opties. Zo kan je bijvoorbeeld een bepaalde taak aan een bepaalde “core” toewijzen en zo “echte” synchrone taken uitvoeren.

### Sectie 2.03 Case system

Case nr. | Sensors | L | ML | M | MR | R | Dist
1 | ExtremeLeft | ON | OFF | OFF | OFF | OFF | OFF
2 | HardLeft | ON | ON | OFF | OFF | OFF | OFF
3 | MediumLeft | OFF | ON | OFF | OFF | OFF | OFF
4 | SoftLeft | OFF | ON | ON | OFF | OFF | OFF
5 | Strait | OFF | OFF | ON | OFF | OFF | OFF
6 | SoftRight | OFF | OFF | ON | ON | OFF | OFF
7 | MediumRight | OFF | OFF | OFF | ON | OFF | OFF
8 | HardRight | OFF | OFF | OFF | ON | ON | OFF
9 | ExtremeRight | OFF | OFF | OFF | OFF | ON | OFF
10 | CrossLine | ON | ON | ON | ON | ON | OFF
11 | LOSTLine | OFF | OFF | OFF | OFF | OFF | OFF
12 | Objectdetect | OFF | OFF | OFF | OFF | OFF | ON

In de programmatie test de microcontroller de sensorwaarde voor verschillende cases. Aan de hand van deze waarde wordt er een “casenummer” gegeven. Deze kan dan worden opgevraagd door een andere taak, in dit geval de motor sturing taak (taskstep).

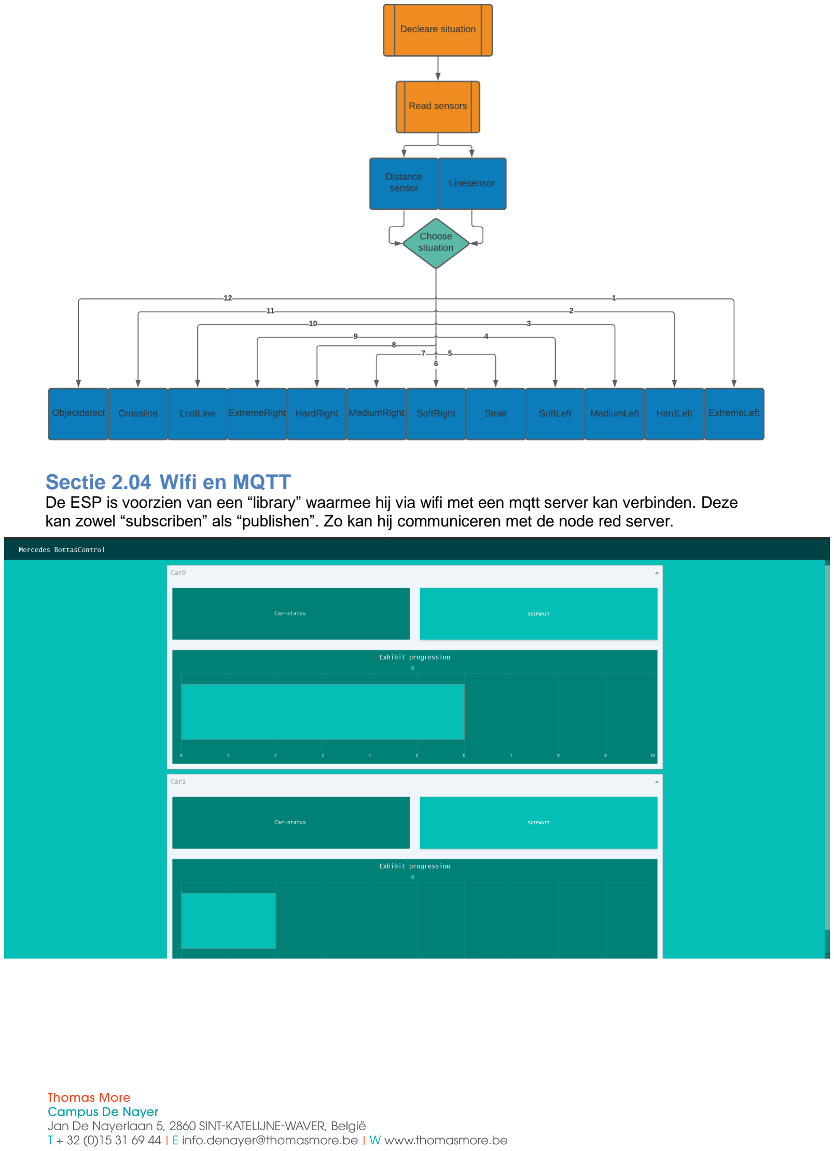
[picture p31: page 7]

### Sectie 2.04 Wifi en MQTT

De ESP is voorzien van een “library” waarmee hij via wifi met een mqtt server kan verbinden. Deze kan zowel “subscriben” als “publishen”. Zo kan hij communiceren met de node red server.


## Artikel III. Tutorial

### Sectie 3.01 Prerequisites

Tijdens de tutorial wordt ervan uitgegaan dat er kennis is van volgende elementen:
- Elektronica
- Mechanica
- ESP32 en software
- MQTT
- Node Red
- Netwerken

### Sectie 3.02 Stap 1: Acquiring hardware

De eerste stap om het wagentje te bouwen is natuurlijk alle hardware en elektronica aan te kopen. Deze onderdelen werden eerder in dit document beschreven onder het deel hardware en zijn ook terug te vinden in de BOM.

### Sectie 3.03 Stap 2: Assemblage

Nadat alle onderdelen zijn aangekomen, kunnen we beginnen met de assemblage van de wagentjes.

(a) Bodem frame
Bevestig de motor houders, zwenkwieltjes en batterijhouder aan het bodem frame met de bijhorende bouten, moeren en rondellen.
(b) Midden frame
Bevestig de stapper motoren in de motorhouders. Installeer de “support poles” op de bodemplaat. Installeer ook de bumper met line sensor.
(c) Boven frame
Installeer het boven frame op de “support poles” en bevestig deze. Installeer vervolgens de mounting bracket voor de afstandssenor.

(d) PCB
Soldeer alle componenten op de PCB behalve de motorkabels.
(e) Elektronica bevestigen
Bevestig de servo op het mounting bracket. Neem de afstand sensor en installeer deze op het bovendeel van het mounting bracket en installeer het geheel vervolgens op de servomotor. Bevestig vervolgens de pcb met de bijhorende bouten, moeren en “standoffs” op het boven frame.
(f) Afmontage Elektronica
Tot slot worden alle kabels getrokken en verbonden met de bijhorende onderdelen volgens onderstaand schema.

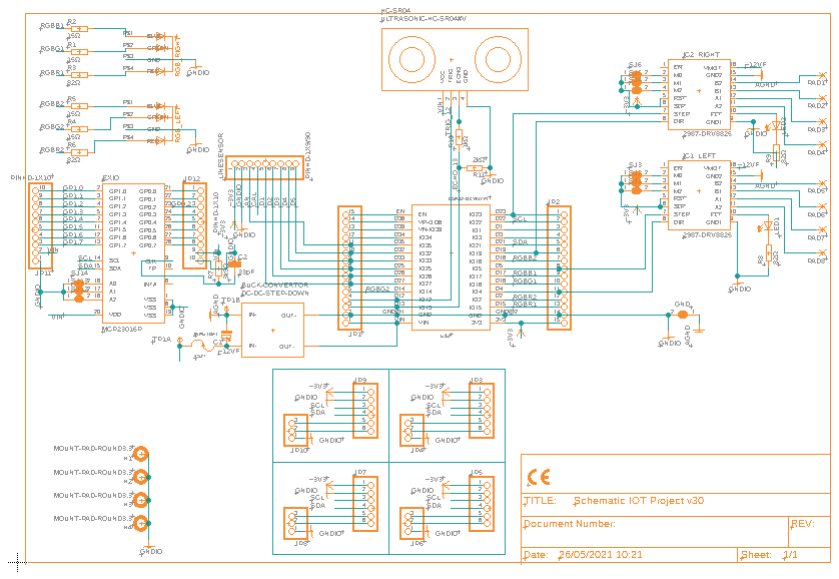
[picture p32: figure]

### Sectie 3.04 Stap 3: MQTT and node red

Installeer een MQTT en Node Red server. Hierbij kan gebruik gemaakt worden van een raspberry pi. Installeer de node-red flow voor de wagensturing.

### Sectie 3.05 Stap 4: Programmatie ESP32

Nu we een MQTT-server hebben, moeten we de ESP32 programmeren. Vergeet niet voor het programmeren de code aan te passen aan de huidige situatie (wifi ssid, password, etc.). Programmeer vervolgens ESP.

### Sectie 3.06 Stap 5 Aanleggen van het parcours

Het aanleggen van het parcours kan simpelweg worden gedaan door het trekken van een zwarte lijn op lichte grond of witte lijn op donkere grond. Vervolgens kunnen er dwarslijnen voorzien worden om het wagentje te stoppen op de “points of intrest”.

### Sectie 3.07 Stap 6 Tewerkstelling

Tot slot kunnen de wagentjes in werking worden gesteld. Door deze op de lijn te plaatsen en de batterij in te steken.

## Artikel IV. Resources

https://grabcad.com/library/esp-wroom-32-2https://www.cytron.io/p-maker-line-simplifying-line-sensor-for-beginnerhttps://www.jkongmotor.com/product/42HS-NEMA17-2Phas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 (https://www.makerguides.com/wp-content/uploads/2019/02/DRV8825-Arduino-stepper-motor-wiring-schematic-diagram-pinout_bb-1024x551.jpg) https://www.makerguides.com/drv8825-stepper-motor-driver-arduino-tutorial/https://github.com/suzakulab/Eagle-Library-Pololuhttps://www.diymodules.org/eagle-show-obje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 (https://www.diymodules.org/eagle-show-object?type=dm&file=diy-modules.lbr&device=DC-DC-STEP-DOWN-MP2307)
https://www.airspayce.com/mikem/arduino/AccelStepper/index.htmlhttps://www.microchip.com/wwwproducts/en/MCP23016https://www.instructables.com/IO-Expander-for-ESP32-E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
https://www.studiopieters.nl/esp32-pinout/https://flows.nodered.org/node/node-red-dashboard

Colors:
#004146 | RGB (0,65,70)

#018076 | RGB (1,128,118)

#03BFB5 | RGB (3,191,181)

#949398 | RGB (148,147,152)

#EFF5F9 | RGB (239,245,249)

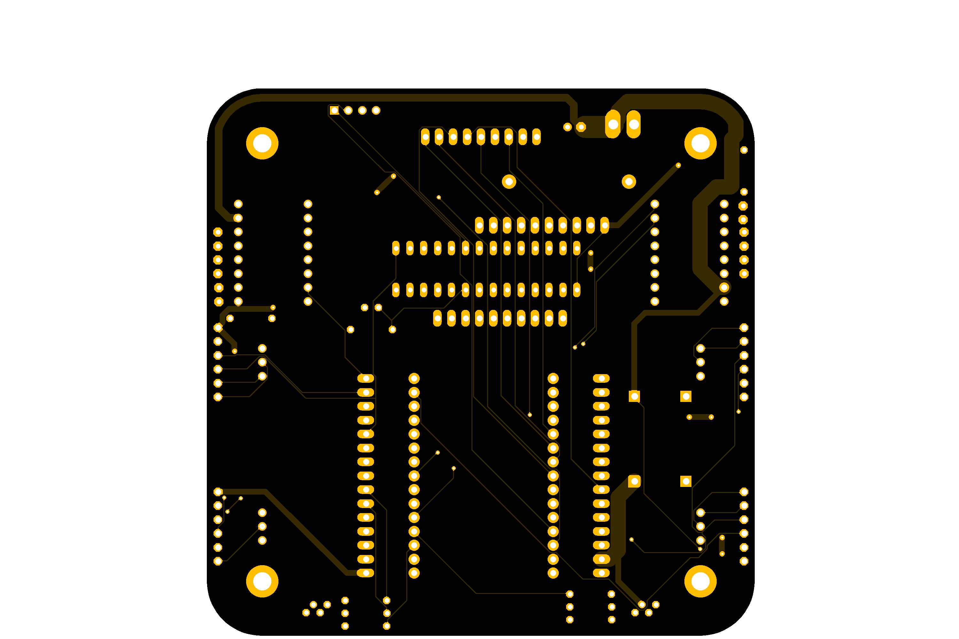
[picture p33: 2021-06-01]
Pictures/Electronics/Schematic IOT Project.bottom.png

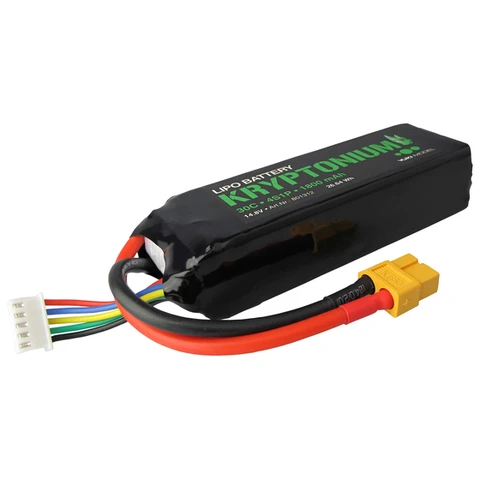
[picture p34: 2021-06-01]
Pictures/Electronics/lipo-4s1p-148v-1800mah-30c-kryptonium-xt60_1_large.png

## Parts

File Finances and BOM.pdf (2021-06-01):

Item | Discription | Price Qty
Cytron Maker Line | Simplifying Line Sensor for BeginnersSKU: 19064 | 11,95 € | 1
Shipping Sensor | Shipping elektor | | 1
PCB mainboard | PCB robot driver board | 0,51 € | 1
SHIPPING CHARGE | SHIPPING | | 1
PAYPAL FEE | PAYPAL FEE | | 1
DRV8825 driver | DSD00010 _Stepstick DRV8825 drive with heatsink | 5,00 € | 2
Inbusstelschroef M4x5 | DBM00194 _Inbusstelschroef M4x5 (10 stuks) | 2,30 € | 1
Verzend- en administratiekosten | Verzend- en administratiekosten 123-3D.nl | | 1
Lipo Battery | Yuki Kryptonium 3S 11.1V 30C 5000mAh LiPo 801323 | 45,99 € | 1
Step-Down Buck Converter | DEBO DCDC DOWN 4 (mini 360) | 2,02 € | 1
Dupont kit | Dupont connector kit | 5,00 € | 1
Fuse holder | fuse holder | 0,30 € | 1
Fuse | fuse 2A | 0,20 € | 1
RGB led | RGB common cathode | 1,03 € | 2
3mm led | 3mm led red | 0,05 € | 2
Resistors | resistors various values | 0,02 € | 8
HC-SR04 | HC-SR04 Ultrasonic sensor – afstandsmeter | 3,00 € | 1
capacator | capacator | 0,11 € | 2
3D print | 3d prints materiaal+manafacturing | 20,00 € | 1
Lasercut frame | laserkcut frame matriaal+manafacturing | 20,00 € | 1
Stepper motor | JK42HS34-1334 | 13,00 € | 2
Hardware | varous nuts and bolts | 15,00 € | 1
Knikkers | knikkers | 0,20 € | 2

Extra costs | Total
| 11,95 €
7,95 € | 7,95 €
| 0,51 €
12,63 € | 12,63 €
0,41 € | 0,41 €
| 10,00 €
| 2,30 €
5,95 € | 5,95 €
| 45,99 €
| 2,02 €
| 5,00 €
| 0,30 €
| 0,20 €
| 2,06 €
| 0,10 €
| 0,13 €
| 3,00 €
| 0,22 €
| 20,00 €
| 20,00 €
| 26,00 €
| 15,00 €
| 0,40 €
| 192,12 €

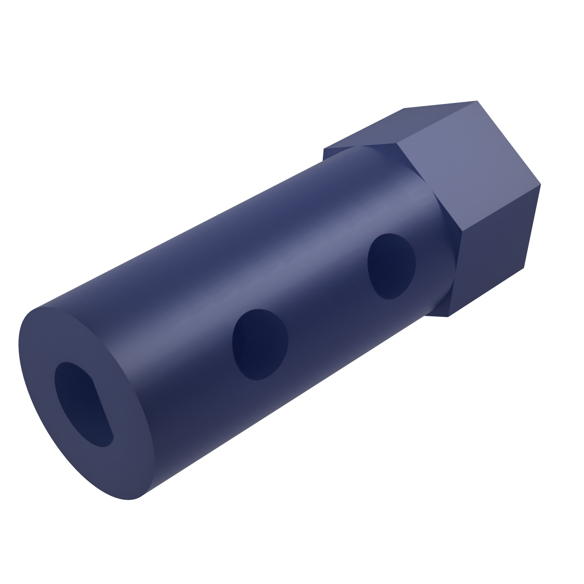
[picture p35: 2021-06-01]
Pictures/3D_printed_parts/Frame_2021-May-28_12-12-56PM-000_CustomizedView17679633802.png

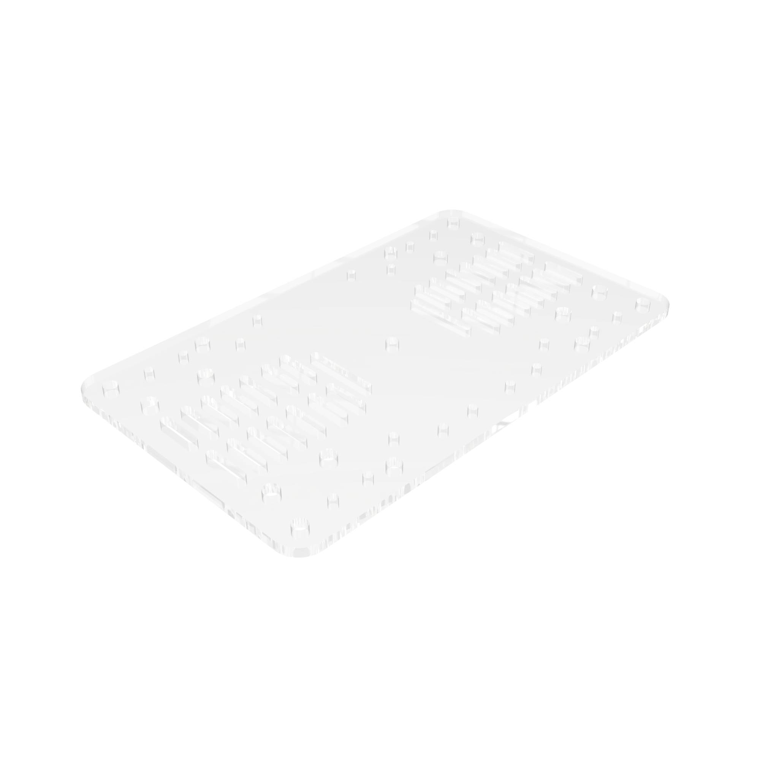
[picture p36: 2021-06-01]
Pictures/Laser_cut_parts/Frame_v1_2021-May-03_02-14-52PM-000_CustomizedView3194152419.png

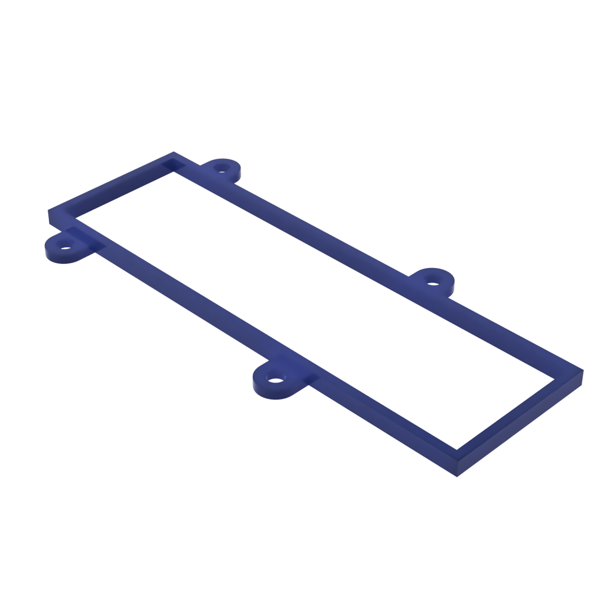
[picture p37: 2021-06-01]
Pictures/3D_printed_parts/Frame_2021-May-28_12-17-25PM-000_CustomizedView8038390272.png

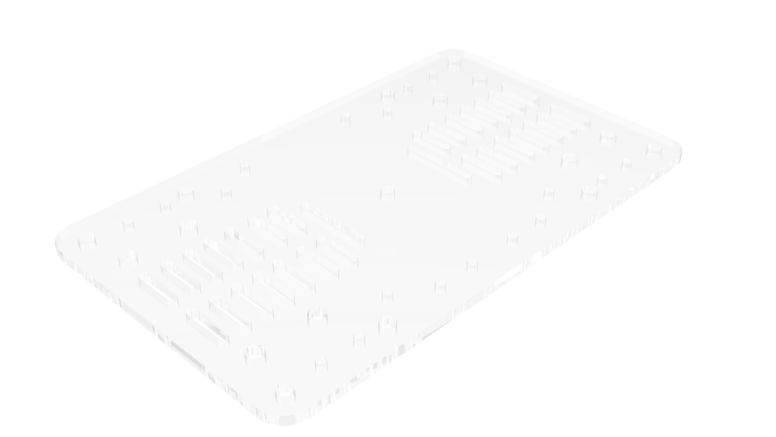
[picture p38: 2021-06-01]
Pictures/Laser_cut_parts/Frame_2021-May-28_12-16-27PM-000_CustomizedView1499520323.png

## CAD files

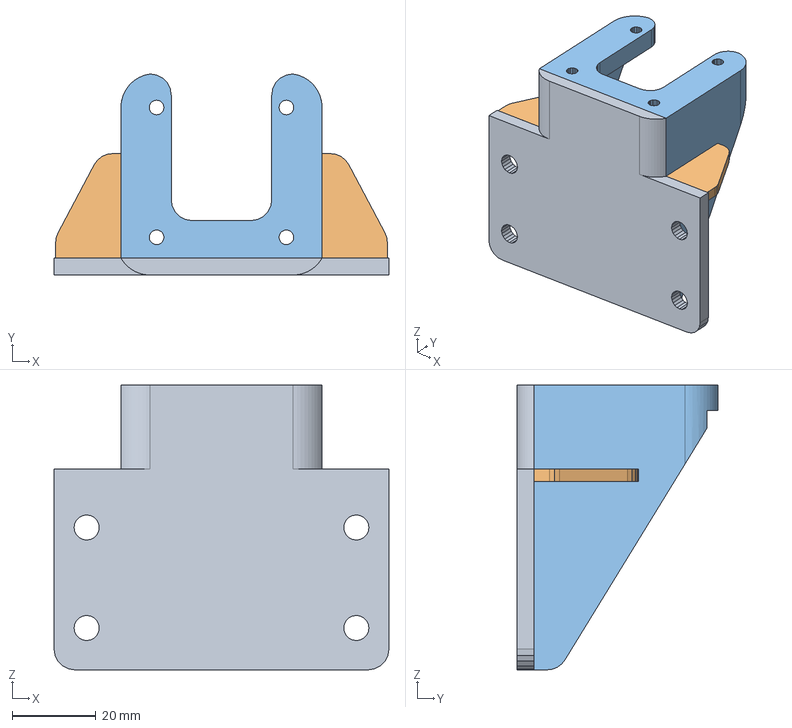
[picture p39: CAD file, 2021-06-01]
Step_and_stl_files/nema17bracket_v2 v3.step
80.0 x 48.0 x 68.0 mm

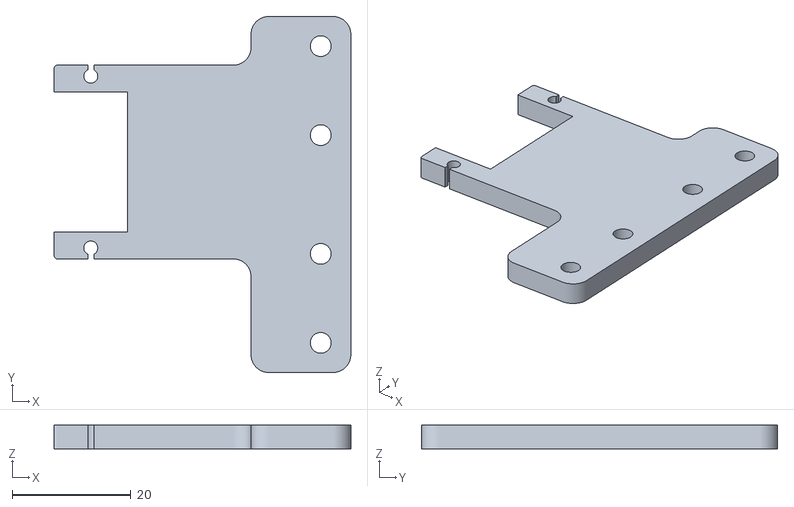
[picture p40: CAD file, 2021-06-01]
Step_and_stl_files/Hcsr04_holder3.stl
50.0 x 60.0 x 4.00

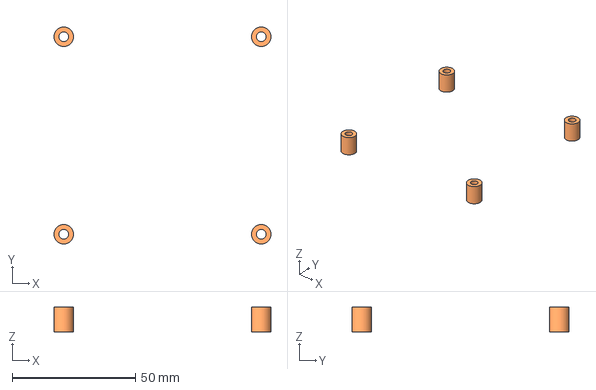
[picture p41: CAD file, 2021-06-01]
Step_and_stl_files/Standoff pcb.step
87.9 x 87.9 x 10.0 mm

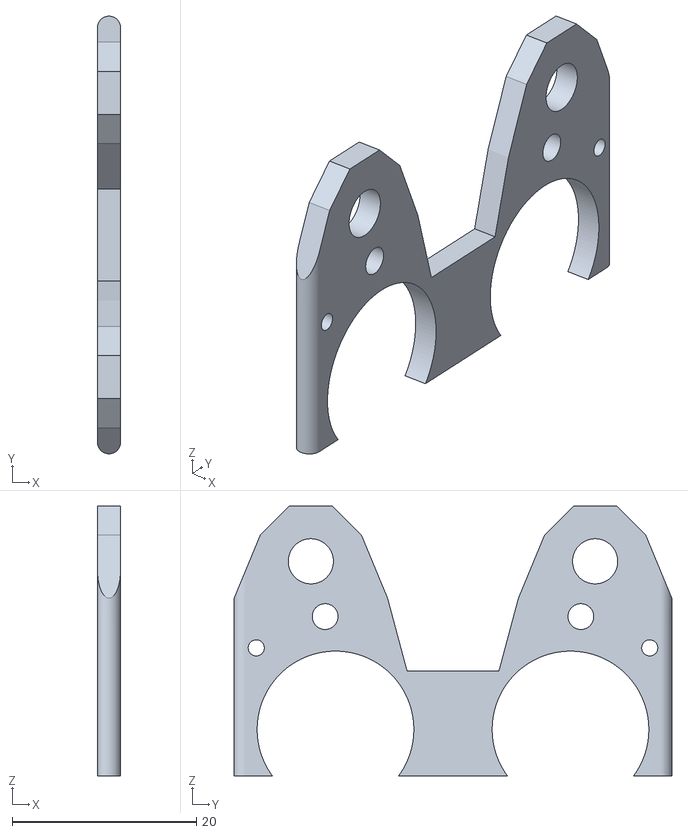
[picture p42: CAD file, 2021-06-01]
Step_and_stl_files/Hcsr04_holder1.stl
2.50 x 47.5 x 29.3

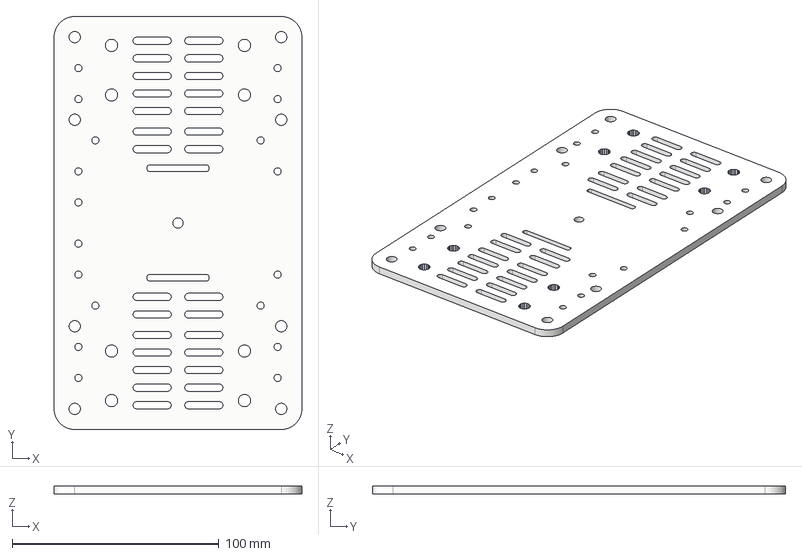
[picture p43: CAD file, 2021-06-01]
Step_and_stl_files/Top Frame.step
120.0 x 200.0 x 4.00 mm

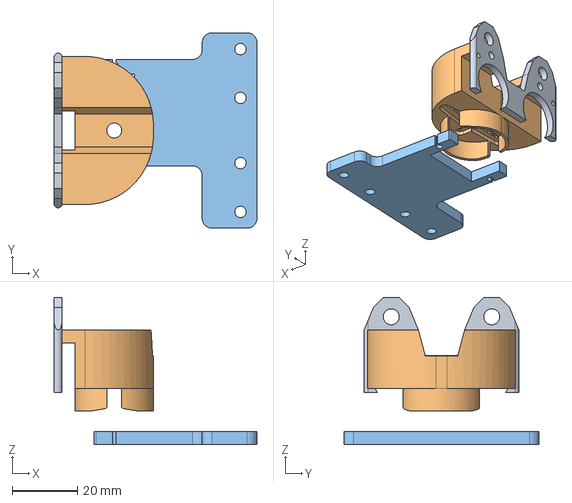
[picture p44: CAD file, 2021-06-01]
Step_and_stl_files/Hcsr04_holder.step
62.3 x 60.0 x 45.3 mm

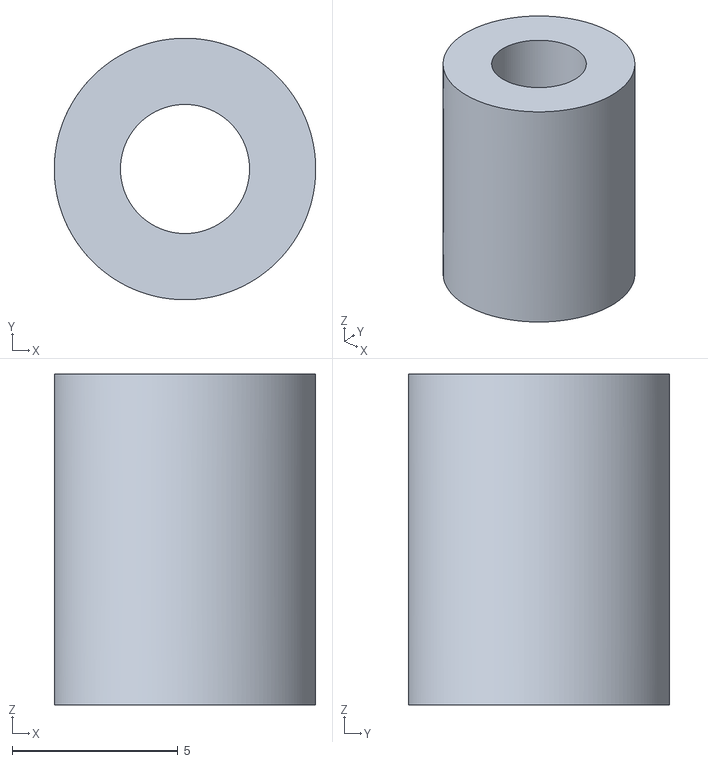
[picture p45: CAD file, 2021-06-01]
Step_and_stl_files/Standoff.stl
7.90 x 7.90 x 10.0

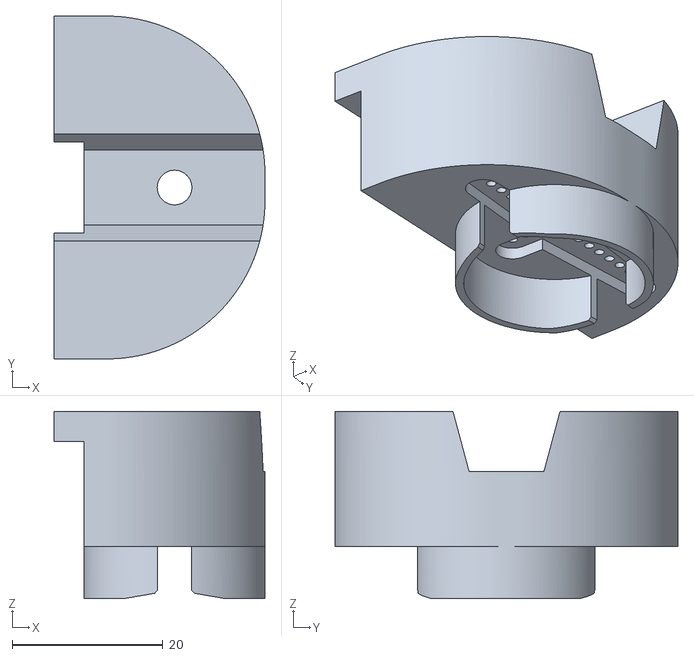
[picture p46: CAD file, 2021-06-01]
Step_and_stl_files/Hcsr04_holder2.stl
28.0 x 45.5 x 24.8

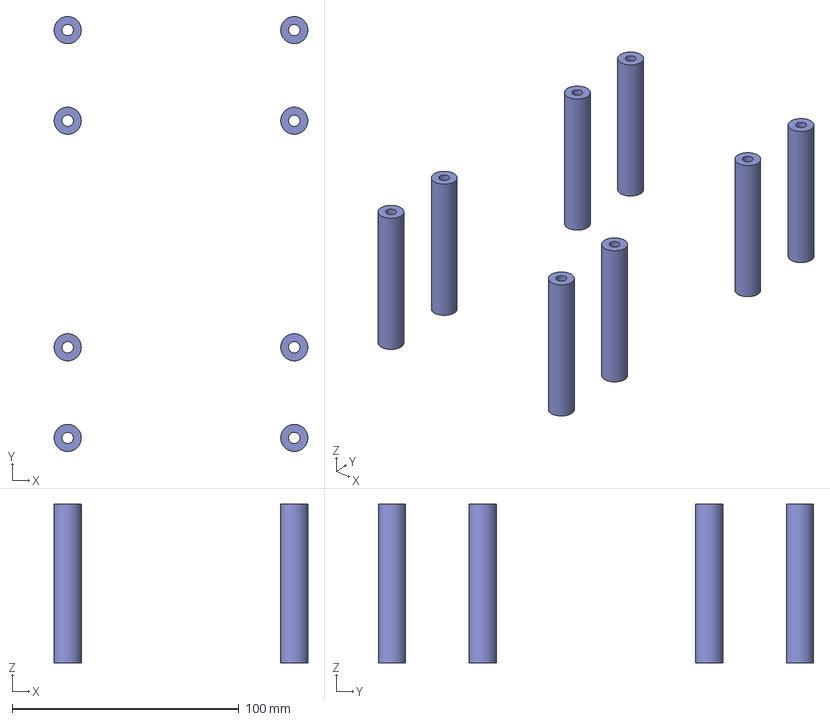
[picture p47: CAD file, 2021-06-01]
Step_and_stl_files/Support poles.step
112.0 x 192.0 x 70.0 mm

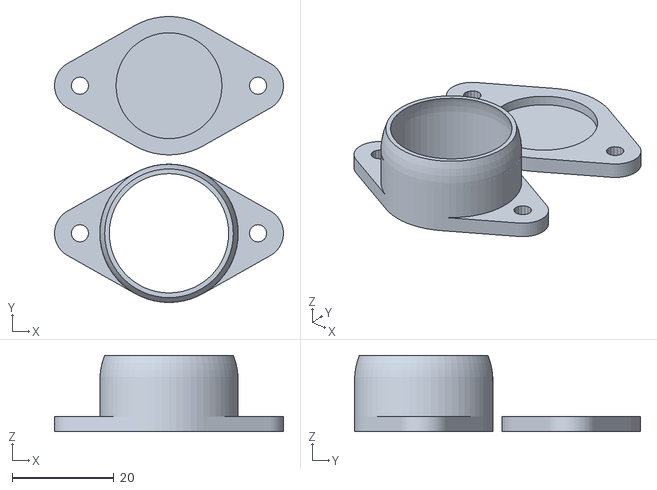
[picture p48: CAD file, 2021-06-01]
Step_and_stl_files/ball_caster_24mm_ball_33height.stl
45.0 x 56.2 x 15.0

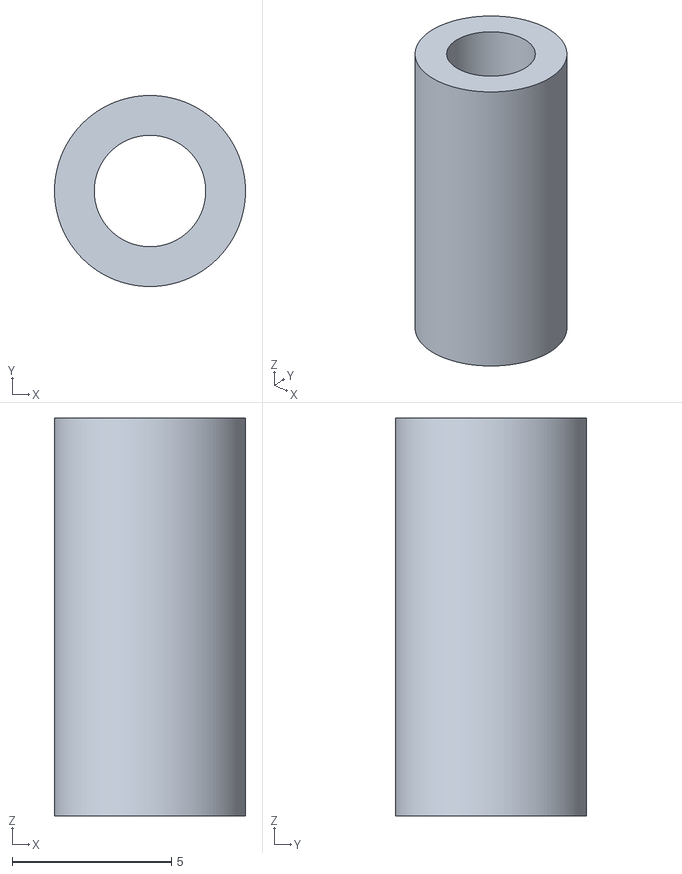
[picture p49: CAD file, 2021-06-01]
Step_and_stl_files/Bumper3.stl
6.00 x 6.00 x 12.5

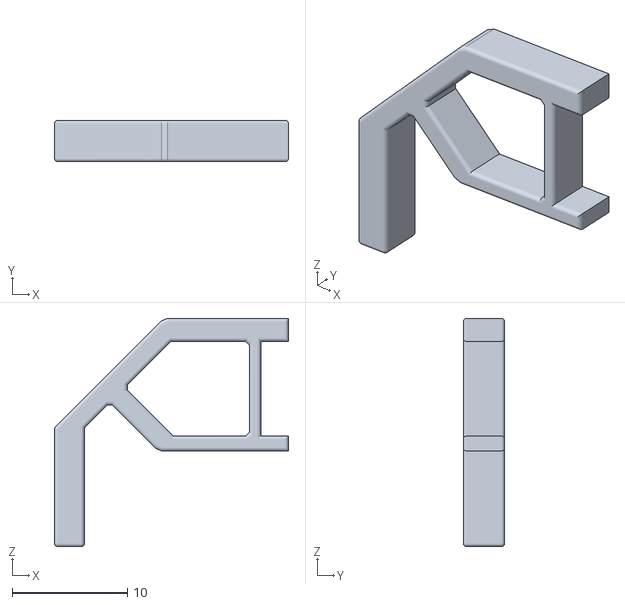
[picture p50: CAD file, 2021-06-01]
Step_and_stl_files/Bumper2.stl
20.3 x 3.60 x 19.8

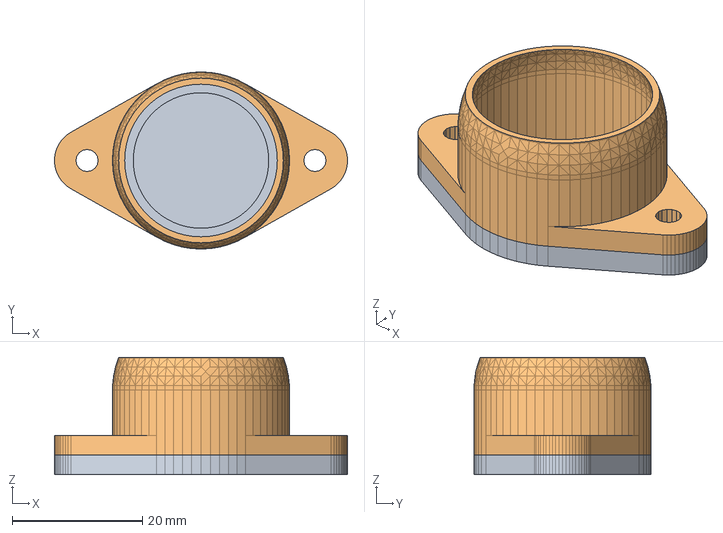
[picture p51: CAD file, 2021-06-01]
Step_and_stl_files/ball_caster_24mm_ball_33height v4.step
45.0 x 27.2 x 18.0 mm

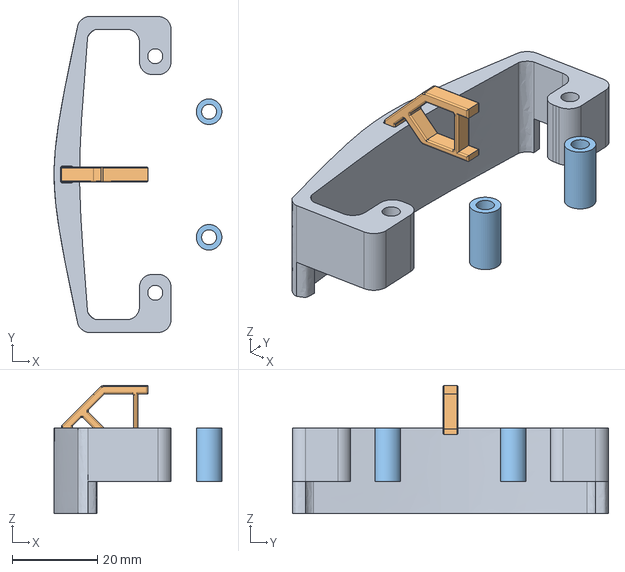
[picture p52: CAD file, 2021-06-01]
Step_and_stl_files/Bumperbar.step
39.3 x 74.0 x 30.0 mm

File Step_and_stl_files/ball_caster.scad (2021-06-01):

//Ball caster.
//Parametric.
//Oktay Gülmez, 24/2/2016.
//GNU_GPL_V3


//Parameters:
//Diameter of the marble in mm.
ball_diameter=24;
//Desired height: (Minimum=ball_diameter+2mm.)
caster_height=33;
//Distance of the mounting holes center in mm.
mountingHoles_width=35;
//Diameter of the mounting screws. 2 for M2, 3 for M3.
mountingScrew_dia=3;
//Nozzle diameter of your printer's in mm.
nozzle_dia=0.4;
//Diameter of the Washer for reducing friction in mm.
washer_dia=20;
//Thickness of the Washer for reducing friction in mm.
washer_thickness=1.9;

$fn=60;
difference(){
    union(){
 //Body: 
       translate([0,0,0]) cylinder(h=ball_diameter/2-2, r=ball_diameter/2+4*nozzle_dia); 
       translate([0,0,ball_diameter/2-2]) sphere(r=ball_diameter/2+4*nozzle_dia);  
 //Mounting:       
        linear_extrude(height = 3, convexity = 10) hull() {
   translate([-mountingHoles_width/2,0,0])circle(5);
   translate([0,0,0]) circle(ball_diameter/2+4*nozzle_dia);
        }
        linear_extrude(height = 3, convexity = 10) hull() {
   translate([0,0,0])circle(ball_diameter/2+4*nozzle_dia);
   translate([mountingHoles_width/2,0,0]) circle(5);
        }
 //Spacer:      
        linear_extrude(height = caster_height-ball_diameter, convexity = 10, $fn=60) hull() {
   translate([-mountingHoles_width/2,ball_diameter+5,0])circle(5);
   translate([0,ball_diameter+5,0]) circle(ball_diameter/2+4*nozzle_dia);
        }
        linear_extrude(height = caster_height-ball_diameter, convexity = 10, $fn=60) hull() {
   translate([0,ball_diameter+5,0])circle(ball_diameter/2+4*nozzle_dia);
   translate([mountingHoles_width/2,ball_diameter+5,0]) circle(5);
        }
        
    }
    
//Top cut:   
    translate([-ball_diameter/2-2,-ball_diameter/2-2,ball_diameter/2+3]) cube([ball_diameter+4,ball_diameter+4,10]);
//Inside:    
    translate([0,0,-5]) cylinder(h=ball_diameter/2+4, r=ball_diameter/2+nozzle_dia); 
    translate([0,0,ball_diameter/2-1]) sphere(r=ball_diameter/2+nozzle_dia);  
//Mounting holes:    
    translate([-mountingHoles_width/2,0,-1]) cylinder(h=caster_height, r=mountingScrew_dia/2+nozzle_dia/2,$fn=16); 
    translate([mountingHoles_width/2,0,-1]) cylinder(h=caster_height, r=mountingScrew_dia/2+nozzle_dia/2,$fn=16); 
    
    translate([-mountingHoles_width/2,ball_diameter+5,-1]) cylinder(h=caster_height, r=mountingScrew_dia/2+nozzle_dia/2,$fn=16); 
    translate([mountingHoles_width/2,ball_diameter+5,-1]) cylinder(h=caster_height, r=mountingScrew_dia/2+nozzle_dia/2,$fn=16);
//Washer area:   
    translate([0,ball_diameter+5,caster_height-ball_diameter-washer_thickness]) cylinder(h=2*washer_thickness, r=washer_dia/2+nozzle_dia); 


}

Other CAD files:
Step_and_stl_files/ball_caster_24mm_ball_33height_1.stl
Step_and_stl_files/ball_caster_24mm_ball_33height_2.stl
Step_and_stl_files/ball_caster_25mm_ball_27height.stl
Step_and_stl_files/ball_caster_25mm_ball_27height_2.stl
Step_and_stl_files/Batt holder.f3d
Step_and_stl_files/Batt holder.step
Step_and_stl_files/Batt holder.stl
Step_and_stl_files/Bottom Frame.dxf
Step_and_stl_files/Bottom Frame.f3d
Step_and_stl_files/Bottom Frame.step
Step_and_stl_files/Bumper1.stl
Step_and_stl_files/Bumper4.stl
Step_and_stl_files/Bumperbar.f3d
Step_and_stl_files/Coupler v8.f3d
Step_and_stl_files/Coupler v8.step
Step_and_stl_files/Coupler v8.stl
Step_and_stl_files/Hcsr04_holder.f3d
Step_and_stl_files/Standoff pcb.f3d
Step_and_stl_files/Support poles.f3d
Step_and_stl_files/Support poles.stl
Step_and_stl_files/Top Frame.f3d
Step_and_stl_files/Top_frame.dxf
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

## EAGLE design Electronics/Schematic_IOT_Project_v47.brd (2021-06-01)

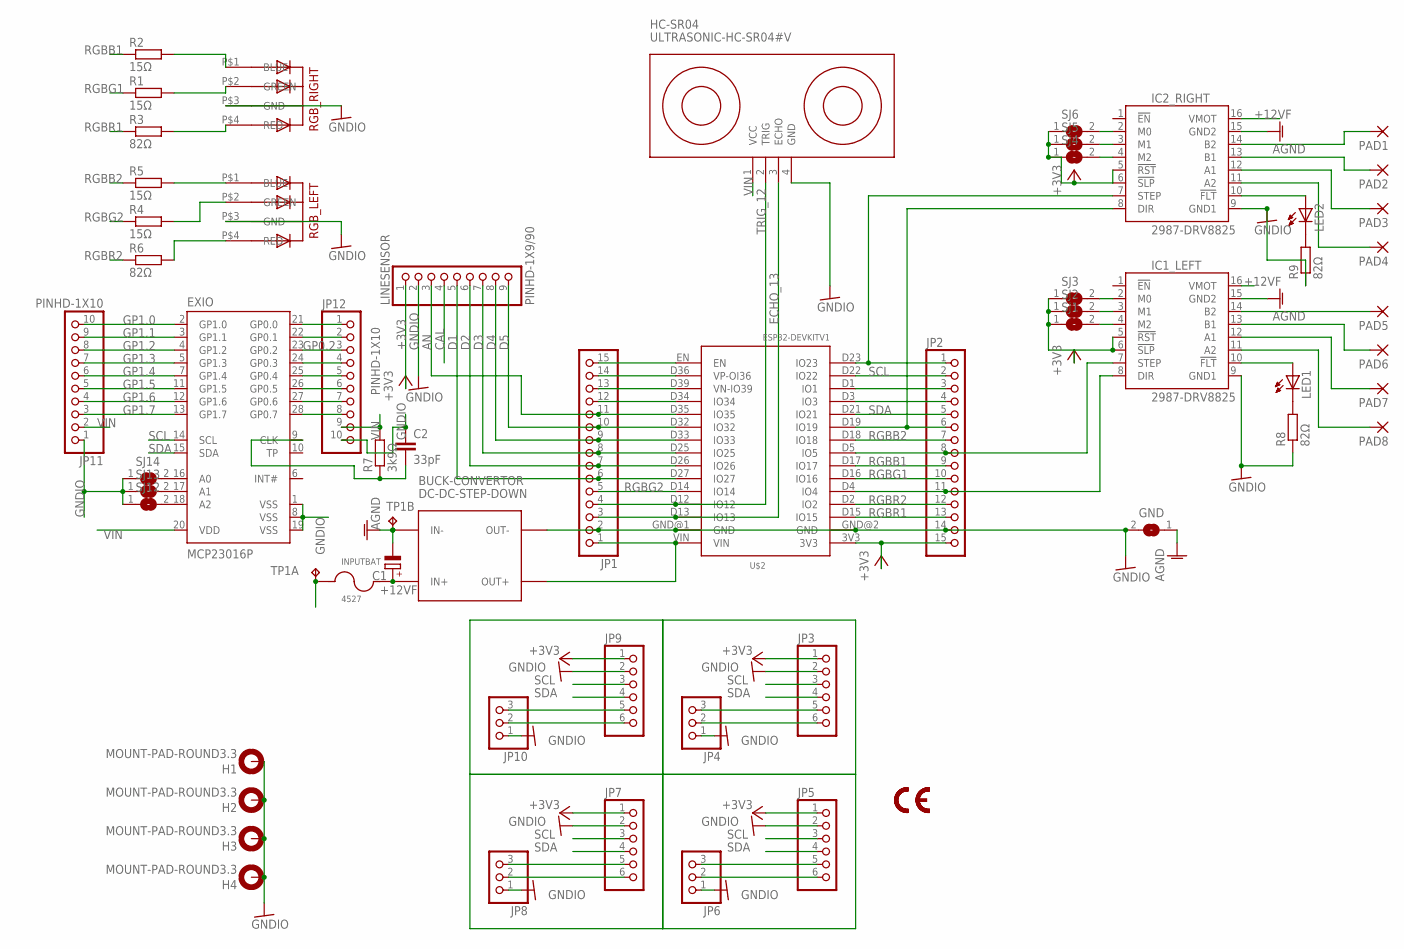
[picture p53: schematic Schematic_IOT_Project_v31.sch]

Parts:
BUCK-CONVERTOR: DC-DC-STEP-DOWN; DC-DC-STEP-DOWN-MP2307
C1: CPOL-EUE2,5-6E; E2,5-6E
C2: 33pF; C025-024X044
EXIO: MCP23016P; DIL28-3
GND: SJ
H1, H2, H3, H4: MOUNT-PAD-ROUND3.3; 3,3-PAD
HC-SR04: ULTRASONIC-HC-SR04#V
IC1_LEFT, IC2_RIGHT: 2987-DRV8825; DRV8825
INPUTBAT: 4527
JP1, JP2: PINHD-1X15; 1X15
JP3, JP5, JP7, JP9: PINHD-1X6; 1X06
JP4, JP6, JP8, JP10: PINHD-1X3; 1X03
JP11, JP12: PINHD-1X10; 1X10
LED1, LED2: LED3MM
LINESENSOR: PINHD-1X9/90; 1X09/90
PAD1, PAD2, PAD3, PAD4, PAD5, PAD6, PAD7, PAD8: 1,6/0,8
R1, R2, R4, R5: 15Ω; 0204/7
R3, R6, R8, R9: 82Ω; 0204/7
R7: 3k9Ω; 0204/7
RGB_LEFT: 5MMRGBLED; LED5MMRGB
RGB_RIGHT: 5MMRGBLED; LED5MMRGB
SJ1, SJ2, SJ3, SJ4, SJ5, SJ6, SJ12, SJ13, SJ14: SJ
TP1: TP2P2-38-17; P2-38-17
U$2: ESP32DEVKITV1; ESP32-DEVKITV1

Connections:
+3V3: IC1_LEFT.5 (!RST), IC1_LEFT.6 (!SLP), IC2_RIGHT.5 (!RST), IC2_RIGHT.6 (!SLP), JP2.15, JP3.1, JP5.1, JP7.1, JP9.1, LINESENSOR.1, SJ1.1, SJ2.1, SJ3.1, SJ4.1, SJ5.1, SJ6.1, U$2.3V3
+12VF: BUCK-CONVERTOR.IN+, C1.+, IC1_LEFT.16 (VMOT), IC2_RIGHT.16 (VMOT), INPUTBAT.2
AGND: BUCK-CONVERTOR.IN-, C1.-, GND.1, IC1_LEFT.15 (GND2), IC2_RIGHT.15 (GND2), TP1.TP-2
AN: JP1.11, LINESENSOR.3, U$2.D35 (IO35)
CAL: LINESENSOR.4
D1: JP1.6, LINESENSOR.5, U$2.D27 (IO27)
D2: JP1.7, LINESENSOR.6, U$2.D26 (IO26)
D3: JP1.8, LINESENSOR.7, U$2.D25 (IO25)
D4: JP1.9, LINESENSOR.8, U$2.D33 (IO33)
D5: JP1.10, LINESENSOR.9, U$2.D32 (IO32)
ECHO_13: HC-SR04.3 (ECHO), JP1.3, U$2.D13 (IO13)
GNDIO: BUCK-CONVERTOR.OUT-, C2.1, EXIO.1 (VSS), EXIO.8 (VSS), EXIO.19 (VSS), GND.2, H1.B3,3, H2.B3,3, H3.B3,3, H4.B3,3, HC-SR04.4 (GND), IC1_LEFT.9 (GND1), IC2_RIGHT.9 (GND1), JP1.2, JP2.14, JP3.2, JP4.1, JP5.2, JP6.1, JP7.2, JP8.1, JP9.2, JP10.1, JP11.1, JP12.10, LINESENSOR.2, R8.1, R9.1, RGB_LEFT.P$3 (GND), RGB_RIGHT.P$3 (GND), SJ12.1, SJ13.1, SJ14.1, U$2.GND@1 (GND), U$2.GND@2 (GND)
GP0.0: EXIO.21 (GP0.0), JP12.1
GP0.1: EXIO.22 (GP0.1), JP12.2
GP0.2: EXIO.23 (GP0.2), JP12.3
GP0.3: EXIO.24 (GP0.3), JP12.4
GP0.4: EXIO.25 (GP0.4), JP12.5
GP0.5: EXIO.26 (GP0.5), JP12.6
GP0.6: EXIO.27 (GP0.6), JP12.7
GP0.7: EXIO.28 (GP0.7), JP12.8
GP1.0: EXIO.2 (GP1.0), JP11.10
GP1.1: EXIO.3 (GP1.1), JP11.9
GP1.2: EXIO.4 (GP1.2), JP11.8
GP1.3: EXIO.5 (GP1.3), JP11.7
GP1.4: EXIO.7 (GP1.4), JP11.6
GP1.5: EXIO.11 (GP1.5), JP11.5
GP1.6: EXIO.12 (GP1.6), JP11.4
GP1.7: EXIO.13 (GP1.7), JP11.3
IO23: IC2_RIGHT.7 (STEP), JP2.1, U$2.D23 (IO23)
unnamed: R3.2, RGB_RIGHT.P$4 (RED)
unnamed: R1.2, RGB_RIGHT.P$2 (GREEN)
unnamed: IC1_LEFT.7 (STEP), JP2.8, U$2.D5 (IO5)
unnamed: IC2_RIGHT.8 (DIR), JP2.6, U$2.D19 (IO19)
unnamed: R2.2, RGB_RIGHT.P$1 (BLUE)
unnamed: IC1_LEFT.8 (DIR), JP2.11, U$2.D4 (IO4)
unnamed: R4.2, RGB_LEFT.P$2 (GREEN)
unnamed: IC1_LEFT.4 (M2), SJ1.2
unnamed: IC1_LEFT.3 (M1), SJ2.2
unnamed: IC1_LEFT.2 (M0), SJ3.2
unnamed: R5.2, RGB_LEFT.P$1 (BLUE)
unnamed: R6.2, RGB_LEFT.P$4 (RED)
unnamed: IC2_RIGHT.4 (M2), SJ4.2
unnamed: IC2_RIGHT.3 (M1), SJ5.2
unnamed: IC2_RIGHT.2 (M0), SJ6.2
unnamed: IC2_RIGHT.14 (B2), PAD1.1
unnamed: IC2_RIGHT.13 (B1), PAD2.1
unnamed: IC2_RIGHT.12 (A1), PAD3.1
unnamed: IC2_RIGHT.11 (A2), PAD4.1
unnamed: IC1_LEFT.14 (B2), PAD5.1
unnamed: IC1_LEFT.13 (B1), PAD6.1
unnamed: IC1_LEFT.12 (A1), PAD7.1
unnamed: IC1_LEFT.11 (A2), PAD8.1
unnamed: LED1.K (C), R8.2
unnamed: IC1_LEFT.10 (!FLT), LED1.A
unnamed: LED2.K (C), R9.2
unnamed: JP2.3, U$2.D1 (IO1)
unnamed: JP2.4, U$2.D3 (IO3)
unnamed: IC2_RIGHT.10 (!FLT), LED2.A
unnamed: JP1.15, U$2.EN
unnamed: JP1.14, U$2.D36 (VP-OI36)
unnamed: JP1.13, U$2.D39 (VN-IO39)
unnamed: JP1.12, U$2.D34 (IO34)
unnamed: JP5.5, JP6.3
unnamed: JP5.6, JP6.2
unnamed: JP3.5, JP4.3
unnamed: JP3.6, JP4.2
unnamed: JP7.5, JP8.3
unnamed: JP7.6, JP8.2
unnamed: JP9.5, JP10.3
unnamed: JP9.6, JP10.2
unnamed: C2.2, EXIO.9 (CLK), R7.1
unnamed: INPUTBAT.1, TP1.TP-1
unnamed: EXIO.18 (A2), SJ12.2
unnamed: EXIO.17 (A1), SJ13.2
unnamed: EXIO.16 (A0), SJ14.2
RGBB1: JP2.9, R2.1, U$2.D17 (IO17)
RGBB2: JP2.7, R5.1, U$2.D18 (IO18)
RGBG1: JP2.10, R1.1, U$2.D16 (IO16)
RGBG2: JP1.5, R4.1, U$2.D14 (IO14)
RGBR1: JP2.13, R3.1, U$2.D15 (IO15)
RGBR2: JP2.12, R6.1, U$2.D2 (IO2)
SCL: EXIO.14 (SCL), JP2.2, JP3.3, JP5.3, JP7.3, JP9.3, U$2.D22 (IO22)
SDA: EXIO.15 (SDA), JP2.5, JP3.4, JP5.4, JP7.4, JP9.4, U$2.D21 (IO21)
TRIG_12: HC-SR04.2 (TRIG), JP1.4, U$2.D12 (IO12)
VIN: BUCK-CONVERTOR.OUT+, EXIO.20 (VDD), HC-SR04.1 (VCC), JP1.1, JP11.2, JP12.9, R7.2, U$2.VIN

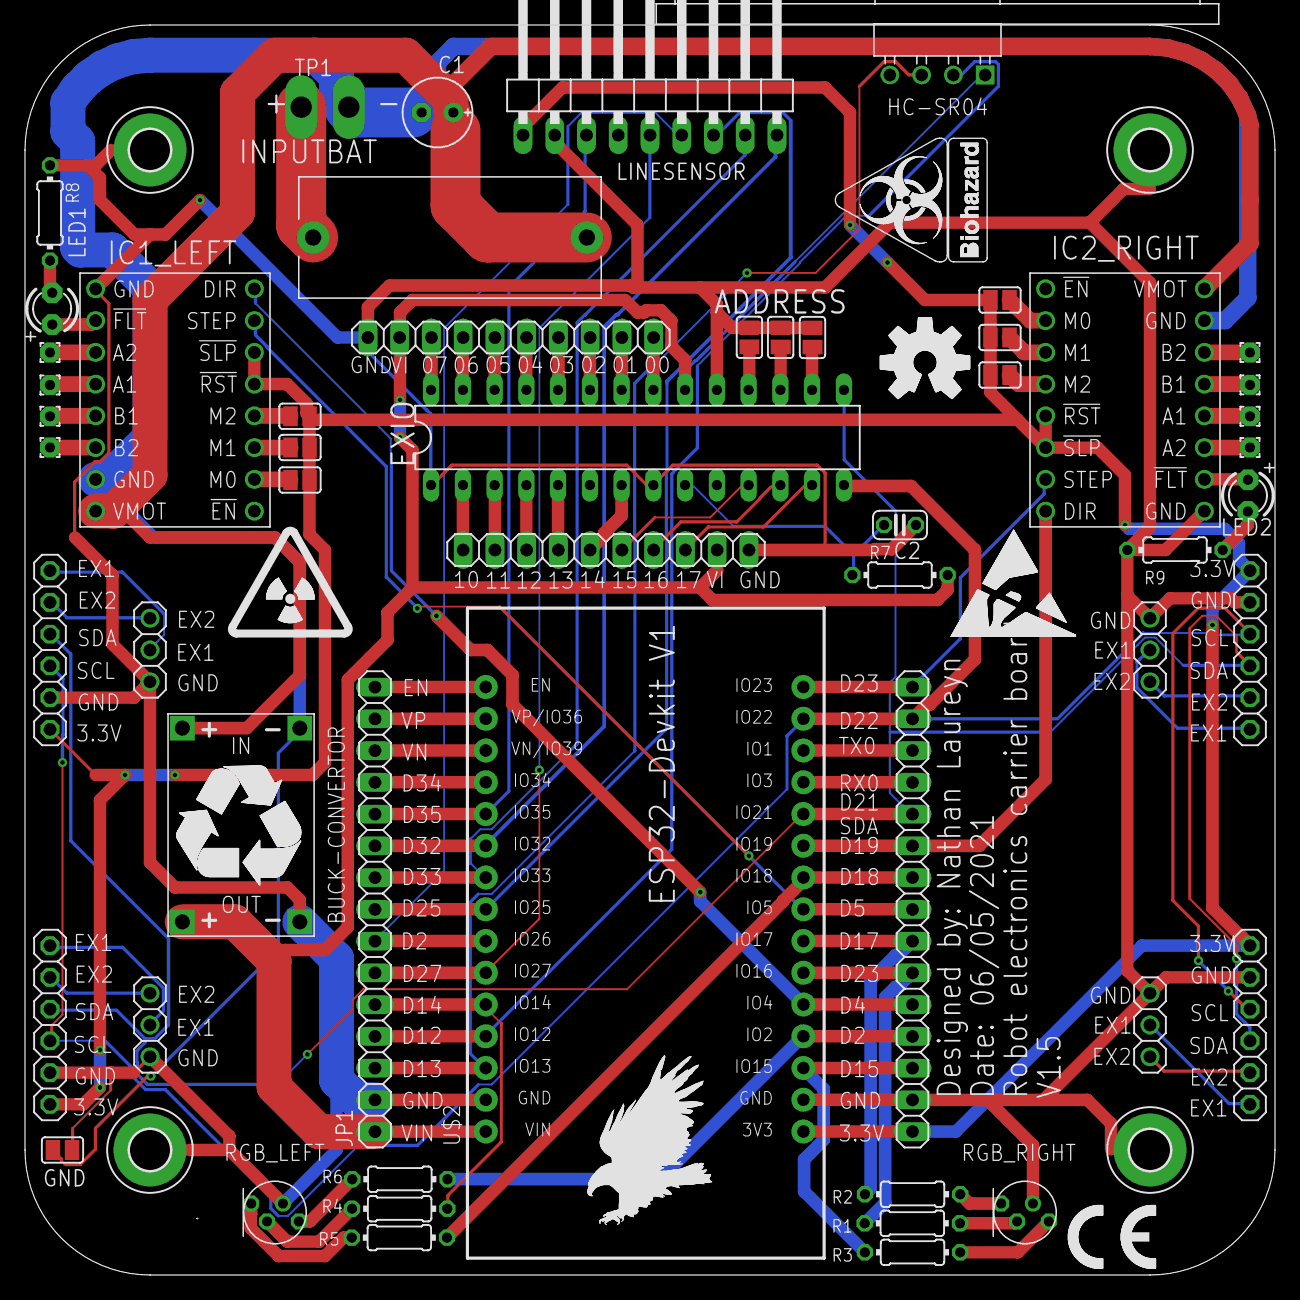
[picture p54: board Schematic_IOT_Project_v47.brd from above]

Board: 2 copper layers, 100.0 x 100.0 mm, 67 parts (0 on the bottom side), 84 nets.

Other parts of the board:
U$1: LOGO
U$3: CE_5MM
U$4: BIOHAZARD_10.00
U$5: ESD_10.00
U$6: OSHW-LOGO-L
U$7: EAGLE-PLC-10MM
U$8: RADIOACTIVE_10.00
U$9: RECYCLING_10.00
U$10: LOGO02

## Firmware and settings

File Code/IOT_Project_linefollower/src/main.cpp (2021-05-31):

//==================================================
/*
Written by: Nathan Laureyn
Version:    v0.2
Date:       08/05/2021
Description:
blablabla
 */
//==================================================

#include <Arduino.h>
#include <AccelStepper.h>
#include <WiFi.h>
#include <PubSubClient.h>

//==================================================

//Wifi Setup==================================================
// MQTT client
const char *ssid = "Protected CEX";
const char *password = "geeninternet";

const char *mqttServer = "192.168.137.187";
const int mqttPort = 1883;
const char *mqttUser = "nqtt";
const char *mqttPassword = "nqtt123";
const char *clientID = "LineFollower";

WiFiClient espClient;
PubSubClient client(espClient);

//Topics
const char *linefollower_status_topic = "home/car/carstatus";
const char *linefollower_control_topic = "home/car/control";

//Payloads
char *CarStatus = "Online";
char *PreviousCarStatus = "Offline";

bool Controloverwrite = false;

//Peripherals==================================================
//Sensorsetup--------------------------------------------------
//Linesensor--------------------------------------------------
//Defines/////////////
//Pins
#define SensL 27  //D1
#define SensML 26 //D2
#define SensM 25  //D3
#define SensMR 33 //D4
#define SensR 32  //D5
//Readmacro's
#define ReadSensL digitalRead(SensL)   //D1
#define ReadSensML digitalRead(SensML) //D2
#define ReadSensM digitalRead(SensM)   //D3
#define ReadSensMR digitalRead(SensMR) //D4
#define ReadSensR digitalRead(SensR)   //D5

//Readsensorcases
//Invert
#define invert == //place == for normal operations and != for inverted operation

//Cases

// ╔═════════╦══════════════╦═════╦═════╦═════╦═════╦═════╦══════╗
// ║ Case nr ║  Sensors=>   ║  L  ║ ML  ║  M  ║ MR  ║  R  ║ Dist ║
// ╠═════════╬══════════════╬═════╬═════╬═════╬═════╬═════╬══════╣
// ║       1 ║ ExtremeLeft  ║ ON  ║ OFF ║ OFF ║ OFF ║ OFF ║ OFF  ║
// ║       2 ║ HardLeft     ║ ON  ║ ON  ║ OFF ║ OFF ║ OFF ║ OFF  ║
// ║       3 ║ MediumLeft   ║ OFF ║ ON  ║ OFF ║ OFF ║ OFF ║ OFF  ║
// ║       4 ║ SoftLeft     ║ OFF ║ ON  ║ ON  ║ OFF ║ OFF ║ OFF  ║
// ║       5 ║ Strait       ║ OFF ║ OFF ║ ON  ║ OFF ║ OFF ║ OFF  ║
// ║       6 ║ SoftRight    ║ OFF ║ OFF ║ ON  ║ ON  ║ OFF ║ OFF  ║
// ║       7 ║ MediumRight  ║ OFF ║ OFF ║ OFF ║ ON  ║ OFF ║ OFF  ║
// ║       8 ║ HardRight    ║ OFF ║ OFF ║ OFF ║ ON  ║ ON  ║ OFF  ║
// ║       9 ║ ExtremeRight ║ OFF ║ OFF ║ OFF ║ OFF ║ ON  ║ OFF  ║
// ║      10 ║ CrossLine    ║ ON  ║ ON  ║ ON  ║ ON  ║ ON  ║ OFF  ║
// ║      11 ║ LOSTLine     ║ OFF ║ OFF ║ OFF ║ OFF ║ OFF ║ OFF  ║
// ║      12 ║ Objectdetect ║ OFF ║ OFF ║ OFF ║ OFF ║ OFF ║ ON   ║
// ╚═════════╩══════════════╩═════╩═════╩═════╩═════╩═════╩══════╝

#define ExtremeLeftSens ReadSensL invert HIGH &&ReadSensML invert LOW &&ReadSensM invert LOW &&ReadSensMR invert LOW &&ReadSensR invert LOW

#define HardLeftSens ReadSensL invert HIGH &&ReadSensML invert HIGH &&ReadSensM invert LOW &&ReadSensMR invert LOW &&ReadSensR invert LOW

#define MediumLeftSens ReadSensL invert LOW &&ReadSensML invert HIGH &&ReadSensM invert LOW &&ReadSensMR invert LOW &&ReadSensR invert LOW

#define SoftLeftSens ReadSensL invert LOW &&ReadSensML invert HIGH &&ReadSensM invert HIGH &&ReadSensMR invert LOW &&ReadSensR invert LOW

#define StraitSens ReadSensL invert LOW &&ReadSensML invert LOW &&ReadSensM invert HIGH &&ReadSensMR invert LOW &&ReadSensR invert LOW

#define SoftRightSens ReadSensL invert LOW &&ReadSensML invert LOW &&ReadSensM invert HIGH &&ReadSensMR invert HIGH &&ReadSensR invert LOW

#define MediumRightSens ReadSensL invert LOW &&ReadSensML invert LOW &&ReadSensM invert LOW &&ReadSensMR invert HIGH &&ReadSensR invert LOW

#define HardRightSens ReadSensL invert LOW &&ReadSensML invert LOW &&ReadSensM invert LOW &&ReadSensMR invert HIGH &&ReadSensR invert HIGH

#define ExtremeRightSens ReadSensL invert LOW &&ReadSensML invert LOW &&ReadSensM invert LOW &&ReadSensMR invert LOW &&ReadSensR invert HIGH

#define CrossLineSens ReadSensL invert HIGH &&ReadSensML invert HIGH &&ReadSensM invert HIGH &&ReadSensMR invert HIGH &&ReadSensR invert HIGH

#define LOSTLineSens ReadSensL invert LOW &&ReadSensML invert LOW &&ReadSensM invert LOW &&ReadSensMR invert LOW &&ReadSensR invert LOW

#define Objectdetectsens cm <= TRG_Point

//DistanceSensorsetup--------------------------------------------------
//Defines/////////////
//Pins

#define TRIGGER_PIN 12 //  pin tied to trigger pin on the ultrasonic sensor.
#define ECHO_PIN 13    //  pin tied to echo pin on the ultrasonic sensor.
#define TRG_Point 40   // Maximum distance we want to ping for (in centimeters). Maximum sensor distance is rated at 400-500cm.
int duration;
int inches;
int cm;

//Buttonsetup--------------------------------------------------
//Defines/////////////
//Pins
#define SkipWaitButton 34 //Pin to be used with skip button

//Led setup--------------------------------------------------

/*
Problem signalisation guide
▪ Green led : No problems
▪ Blue led  : Object detected or crossline
▪ Red led   : Lost line
*/

// Defines some pins the leds will use
#define RGBLrR 15 //D15
#define RGBLgR 16 //D16
#define RGBLbR 17 //D17

#define RGBLrL 2  //D2
#define RGBLgL 14 //D14
#define RGBLbL 18 //D18

#define RGBoff               \
  digitalWrite(RGBLrR, LOW); \
  digitalWrite(RGBLgR, LOW); \
  digitalWrite(RGBLbR, LOW); \
  digitalWrite(RGBLrL, LOW); \
  digitalWrite(RGBLgL, LOW); \
  digitalWrite(RGBLbL, LOW);

//Motorsetup--------------------------------------------------
// Defines some steppers and the pins the motors will use
AccelStepper stepperR(AccelStepper::DRIVER, 23, 19);
AccelStepper stepperL(AccelStepper::DRIVER, 5, 4);
//Speedmacro's
#define StandardSpeed 100                            //sets standard maxspeed
#define StandardAccel 100.0                           //sets standard acceleration
#define StandardLocation currentPosition() - 1000000 //sets standard location

#define ExtremeLeftSpeed StandardSpeed / 1.0000001
#define HardLeftSpeed StandardSpeed / 3
#define MediumLeftSpeed StandardSpeed / 1.5
#define SoftLeftSpeed StandardSpeed / 1.2
#define StraitSpeed StandardSpeed
#define SoftRightSpeed StandardSpeed / 1.2
#define MediumRightSpeed StandardSpeed / 1.5
#define HardRightSpeed StandardSpeed / 3
#define ExtremeRightSpeed StandardSpeed / 1.0000001

#define CrossLineSpeed StandardSpeed - 99.99999
#define LOSTLineSpeed StandardSpeed / 2

int LineStatus;

//Speedcommands
void ExtremeLeft()
{
  stepperR.setMaxSpeed(StandardSpeed);
  stepperL.setMaxSpeed(ExtremeLeftSpeed);
  //stepperR.setAcceleration(StandardAccel);
  //stepperL.setAcceleration(StandardAccel);
  stepperR.moveTo((stepperR.StandardLocation));
  stepperL.moveTo(stepperL.currentPosition());

  RGBoff

      digitalWrite(RGBLgL, HIGH);
  digitalWrite(RGBLgR, LOW);

  //Serial.println("ExtremeLeft");
  CarStatus = "Driving";
}
void HardLeft()
{
  stepperR.setMaxSpeed(StandardSpeed);
  stepperL.setMaxSpeed(HardLeftSpeed);
  //stepperR.setAcceleration(StandardAccel);
  //stepperL.setAcceleration(StandardAccel);
  stepperR.moveTo((stepperR.StandardLocation));
  stepperL.moveTo((stepperL.StandardLocation));

  RGBoff

      digitalWrite(RGBLgL, HIGH);
  digitalWrite(RGBLgR, LOW);

  //Serial.println("HardLeft");
  CarStatus = "Driving";
}
void MediumLeft()
{
  stepperR.setMaxSpeed(StandardSpeed);
  stepperL.setMaxSpeed(MediumLeftSpeed);
  //stepperR.setAcceleration(StandardAccel);
  //stepperL.setAcceleration(StandardAccel);
  stepperR.moveTo((stepperR.StandardLocation));
  stepperL.moveTo((stepperL.StandardLocation));

  RGBoff

      digitalWrite(RGBLgL, HIGH);
  digitalWrite(RGBLgR, LOW);

  //Serial.println("MediumLeft");
  CarStatus = "Driving";
}
void SoftLeft()
{
  stepperR.setMaxSpeed(StandardSpeed);
  stepperL.setMaxSpeed(SoftLeftSpeed);
  //stepperR.setAcceleration(StandardAccel);
  //stepperL.setAcceleration(StandardAccel);
  stepperR.moveTo((stepperR.StandardLocation));
  stepperL.moveTo((stepperL.StandardLocation));

  RGBoff

      digitalWrite(RGBLgL, HIGH);
  digitalWrite(RGBLgR, LOW);

  //Serial.println("SoftLeft");
  CarStatus = "Driving";
}
void Strait()
{
  stepperR.setMaxSpeed(StraitSpeed);
  stepperL.setMaxSpeed(StraitSpeed);
  //stepperR.setAcceleration(StandardAccel);
  //stepperL.setAcceleration(StandardAccel);
  stepperR.moveTo((stepperR.StandardLocation));
  stepperL.moveTo((stepperL.StandardLocation));

  RGBoff

      digitalWrite(RGBLgL, HIGH);
  digitalWrite(RGBLgR, HIGH);

  //Serial.println("Strait");
  CarStatus = "Driving";
}
void SoftRight()
{
  stepperR.setMaxSpeed(SoftRightSpeed);
  stepperL.setMaxSpeed(StandardSpeed);
  //stepperR.setAcceleration(StandardAccel);
  //stepperL.setAcceleration(StandardAccel);
  stepperR.moveTo((stepperR.StandardLocation));
  stepperL.moveTo((stepperL.StandardLocation));

  RGBoff

      digitalWrite(RGBLgL, LOW);
  digitalWrite(RGBLgR, HIGH);

  //Serial.println("SoftRight");
  CarStatus = "Driving";
}
void MediumRight()
{
  stepperR.setMaxSpeed(MediumRightSpeed);
  stepperL.setMaxSpeed(StandardSpeed);
  //stepperR.setAcceleration(StandardAccel);
  //stepperL.setAcceleration(StandardAccel);
  stepperR.moveTo((stepperR.StandardLocation));
  stepperL.moveTo((stepperL.StandardLocation));

  RGBoff

      digitalWrite(RGBLgL, LOW);
  digitalWrite(RGBLgR, HIGH);

  //Serial.println("MediumRight");
  CarStatus = "Driving";
}
void HardRight()
{
  stepperR.setMaxSpeed(HardRightSpeed);
  stepperL.setMaxSpeed(StandardSpeed);
  //stepperR.setAcceleration(StandardAccel);
  //stepperL.setAcceleration(StandardAccel);
  stepperR.moveTo((stepperR.StandardLocation));
  stepperL.moveTo((stepperL.StandardLocation));

  RGBoff

      digitalWrite(RGBLgL, LOW);
  digitalWrite(RGBLgR, HIGH);

  //Serial.println("HardRight");
  CarStatus = "Driving";
}
void ExtremeRight()
{
  stepperR.setMaxSpeed(ExtremeRightSpeed);
  stepperL.setMaxSpeed(StandardSpeed);
  //stepperR.setAcceleration(StandardAccel);
  //stepperL.setAcceleration(StandardAccel);
  stepperR.moveTo(stepperR.currentPosition());
  stepperL.moveTo((stepperL.StandardLocation));

  RGBoff

      digitalWrite(RGBLgL, LOW);
  digitalWrite(RGBLgR, HIGH);

  //Serial.println("ExtremeRight");
  CarStatus = "Driving";
}
void CrossLine()
{
  unsigned long Stoptime = 5000;

  stepperR.setMaxSpeed(CrossLineSpeed);
  stepperL.setMaxSpeed(CrossLineSpeed);
  stepperR.setAcceleration(1000);
  stepperL.setAcceleration(1000);
  stepperR.moveTo(stepperR.currentPosition());
  stepperL.moveTo(stepperL.currentPosition());

  RGBoff

      digitalWrite(RGBLbL, HIGH);
  digitalWrite(RGBLbR, HIGH);
  CarStatus = "Crossline";

  for (int i = 0; i < Stoptime; i++)

  {
    if (digitalRead(SkipWaitButton) == HIGH || Controloverwrite == true)
    {
      i = Stoptime;
      Controloverwrite = false;
    }
    else
    {
      delay(1000);
      i = i + 1000;
    }
    stepperR.setAcceleration(StandardAccel);
    stepperL.setAcceleration(StandardAccel);
  }

  stepperR.setMaxSpeed(StraitSpeed);
  stepperL.setMaxSpeed(StraitSpeed);
  //stepperR.setAcceleration(StandardAccel);
  //stepperL.setAcceleration(StandardAccel);
  stepperR.moveTo((stepperR.StandardLocation));
  stepperL.moveTo((stepperL.StandardLocation));
  delay(500);

  //Serial.println("CrossLine");
}
void LOSTLine()
{
  stepperR.setMaxSpeed(LOSTLineSpeed);
  stepperL.setMaxSpeed(-LOSTLineSpeed);
  stepperR.setAcceleration(1000);
  stepperL.setAcceleration(1000);
  stepperR.moveTo((stepperR.StandardLocation));
  stepperL.moveTo(-(stepperL.StandardLocation));

  RGBoff

      digitalWrite(RGBLrL, HIGH);
  digitalWrite(RGBLrR, HIGH);

  //Serial.println("LOSTLine");
  CarStatus = "Lostline";
}
void Objectdetect()
{
  stepperR.setMaxSpeed(StandardSpeed);
  stepperL.setMaxSpeed(StandardSpeed);
  //stepperR.setAcceleration(StandardAccel);
  //stepperL.setAcceleration(StandardAccel);
  stepperR.moveTo(stepperR.currentPosition());
  stepperL.moveTo(stepperL.currentPosition());
  RGBoff

      digitalWrite(RGBLbL, HIGH);
  digitalWrite(RGBLbR, HIGH);

  //Serial.println("Objectdetect");
  CarStatus = "Objectdetect";
}

void callback(char *topic, byte *payload, unsigned int length)
{

  Serial.print("Message arrived in topic: ");
  Serial.println(topic);
  Serial.print("Message:");

  String messageTemp;
  for (int i = 0; i < length; i++)
  {
    Serial.print((char)payload[i]);
    messageTemp += (char)payload[i];
  }
  Serial.println();

  // Feel free to add more if statements to control more GPIOs with MQTT

  // If a message is received on the topic esp32/output, you check if the message is either "on" or "off".
  // Changes the output state according to the message

  Serial.print("Changing output to ");
  if (messageTemp == "Driveoverwrite")
  {
    Controloverwrite = true;
    Serial.println("-----------------------");
  }

  Serial.println();
  Serial.println("-----------------------");
}

//Tasks==================================================
void taskstep(void *parameters)
{
  for (;;)
  {
    switch (LineStatus)
    {
    case 1:
      ExtremeLeft();
      //Serial.println("	ExtremeLeft	");
      break;
    case 2:
      HardLeft();
      //Serial.println("	HardLeft	");
      break;
    case 3:
      MediumLeft();
      //Serial.println("	MediumLeft	");
      break;
    case 4:
      SoftLeft();
      //Serial.println("	SoftLeft	");
      break;
    case 5:
      Strait();
      //Serial.println("	Strait	");
      break;
    case 6:
      SoftRight();
      //Serial.println("	SoftRight	");
      break;
    case 7:
      MediumRight();
      //Serial.println("	MediumRight	");
      break;
    case 8:
      HardRight();
      //Serial.println("	HardRight	");
      break;
    case 9:
      ExtremeRight();
      //Serial.println("	ExtremeRight	");
      break;
    case 10:
      CrossLine();
      //Serial.println("	CrossLine	");
      break;
    case 11:
      LOSTLine();
      //Serial.println("	LOSTLine	");
      break;
    case 12:
      Objectdetect();
      //Serial.println("	Objectdetect	");
      break;

    default:
      break;
    }

    //Serial.println("steptask");
    vTaskDelay(20 / portTICK_PERIOD_MS);
  }
}

void SensLine(void *parameters)
{

  for (;;)
  {

    if (ExtremeLeftSens)
    {
      LineStatus = 1;
      //Serial.println("	ExtremeLeft	");
    }
    else if (HardLeftSens)
    {
      LineStatus = 2;
      //Serial.println("	HardLeft	");
    }
    else if (MediumLeftSens)
    {
      LineStatus = 3;
      //Serial.println("	MediumLeft	");
    }
    else if (SoftLeftSens)
    {
      LineStatus = 4;
      //Serial.println("	SoftLeft	");
    }
    else if (StraitSens)
    {
      LineStatus = 5;
      //Serial.println("	Strait	");
    }
    else if (SoftRightSens)
    {
      LineStatus = 6;
      //Serial.println("	SoftRight	");
    }
    else if (MediumRightSens)
    {
      LineStatus = 7;
      //Serial.println("	MediumRight	");
    }
    else if (HardRightSens)
    {
      LineStatus = 8;
      //Serial.println("	HardRight	");
    }
    else if (ExtremeRightSens)
    {
      LineStatus = 9;
      //Serial.println("	ExtremeRight	");
    }
    else if (CrossLineSens)
    {
      LineStatus = 10;
      //Serial.println("	CrossLine	");
    }
    else if (LOSTLineSens)
    {
      LineStatus = 11;
      //Serial.println("	LOSTLine	");
    }
    if (Objectdetectsens)
    {
      LineStatus = 12;
      //Serial.println("	Objectdetectsens	");
    }
    //Serial.println("SensLine");
    vTaskDelay(10 / portTICK_PERIOD_MS);
  }
}

void SensDistance(void *parameters)
{

  for (;;)
  {

    // The sensor is triggered by a HIGH pulse of 10 or more microseconds.
    // Give a short LOW pulse beforehand to ensure a clean HIGH pulse:
    digitalWrite(TRIGGER_PIN, LOW);
    delayMicroseconds(5);
    digitalWrite(TRIGGER_PIN, HIGH);
    delayMicroseconds(10);
    digitalWrite(TRIGGER_PIN, LOW);

    // Read the signal from the sensor: a HIGH pulse whose
    // duration is the time (in microseconds) from the sending
    // of the ping to the reception of its echo off of an object.
    pinMode(ECHO_PIN, INPUT);
    duration = pulseIn(ECHO_PIN, HIGH);

    // Convert the time into a distance
    cm = (duration / 2) / 29.1;   // Divide by 29.1 or multiply by 0.0343
    inches = (duration / 2) / 74; // Divide by 74 or multiply by 0.0135

    /* 
   Serial.print(inches);
    Serial.print("in, ");
    Serial.print(cm);
    Serial.print("cm");
    Serial.println();
    */

    vTaskDelay(200 / portTICK_PERIOD_MS);
  }
}

void MQTTPublish(void *parameters)
{

  for (;;)
  {
    if (CarStatus != PreviousCarStatus)
    {
      client.publish(linefollower_status_topic, CarStatus);
      Serial.println(linefollower_status_topic);
      Serial.println(CarStatus);
      PreviousCarStatus = CarStatus;
    }
    vTaskDelay(1000 / portTICK_PERIOD_MS);
  }
}
void MQTTClient(void *parameters)
{

  for (;;)
  {
    client.loop();
    vTaskDelay(10 / portTICK_PERIOD_MS);
  }
}
void setup()
{

  Serial.begin(115200); // initialize the //Serial port:

  WiFi.begin(ssid, password);

  //set up wifi connection=================================================
  while (WiFi.status() != WL_CONNECTED)
  {
    delay(500);
    Serial.println("Connecting to WiFi..");
  }
  Serial.println("Connected to the WiFi network");
  client.setServer(mqttServer, mqttPort);

  // connect to broker
  while (!client.connected())
  {
    Serial.println("Connecting to MQTT...");
    if (client.connect("ESP32Client", mqttUser, mqttPassword))
    {
      Serial.println("connected");
    }
    else
    {
      Serial.print("failed with state ");
      Serial.print(client.state());
      delay(2000);
    }
  }

  //set a callback function for when data is received from broker
  client.setCallback(callback);
  // subscribe to topic
  client.subscribe("home/car/control");

  //pinsetup==================================================
  //linesensor
  pinMode(SensL, INPUT);
  pinMode(SensML, INPUT);
  pinMode(SensM, INPUT);
  pinMode(SensMR, INPUT);
  pinMode(SensR, INPUT);

  //distancesensor
  pinMode(TRIGGER_PIN, OUTPUT);
  pinMode(ECHO_PIN, INPUT);

  //button
  pinMode(SkipWaitButton, INPUT_PULLUP);

  //led
  //RGB R
  pinMode(RGBLrR, OUTPUT); //D15
  pinMode(RGBLgR, OUTPUT); //D16
  pinMode(RGBLbR, OUTPUT); //D17

  //RGB L
  pinMode(RGBLrL, OUTPUT); //D2
  pinMode(RGBLgL, OUTPUT); //D14
  pinMode(RGBLbL, OUTPUT); //D18

  pinMode(LED_BUILTIN, OUTPUT);

  digitalWrite(LED_BUILTIN, HIGH);
  delay(500);
  digitalWrite(LED_BUILTIN, LOW);

  xTaskCreate(
      taskstep,   /* Task function. */
      "taskstep", /* name of task. */
      10000,      /* Stack size of task */
      NULL,       /* parameter of the task */
      1,          /* priority of the task */
      NULL);      /* Task handle to keep track of created task */

  xTaskCreate(
      SensLine,   /* Task function. */
      "SensLine", /* name of task. */
      10000,      /* Stack size of task */
      NULL,       /* parameter of the task */
      1,          /* priority of the task */
      NULL);      /* Task handle to keep track of created task */

  xTaskCreate(
      SensDistance, /* Task function. */
      "SensLine",   /* name of task. */
      10000,        /* Stack size of task */
      NULL,         /* parameter of the task */
      1,            /* priority of the task */
      NULL);        /* Task handle to keep track of created task */
  xTaskCreate(
      MQTTPublish,   /* Task function. */
      "MQTTPublish", /* name of task. */
      10000,         /* Stack size of task */
      NULL,          /* parameter of the task */
      1,             /* priority of the task */
      NULL);         /* Task handle to keep track of created task */
  xTaskCreate(
      MQTTClient,   /* Task function. */
      "MQTTClient", /* name of task. */
      10000,        /* Stack size of task */
      NULL,         /* parameter of the task */
      1,            /* priority of the task */
      NULL);        /* Task handle to keep track of created task */
  //stepperR.setMaxSpeed(StandardSpeed);
  stepperR.setAcceleration(StandardAccel);
  stepperR.moveTo((stepperR.StandardLocation));

  stepperL.setAcceleration(StandardAccel);
  stepperL.moveTo((stepperL.StandardLocation));
}

void loop()
{
  stepperR.run();
  stepperL.run();
}

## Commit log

2021-06-01 Upload of all document files
    [Batt holder.f3d, Batt holder.step, Batt holder.stl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]
2021-06-01 Added missing files
    [Hcsr04_holder.f3d, Hcsr04_holder.step, Hcsr04_holder1.stl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]
2021-06-02 Added node red flow
2021-06-02 Node red flow

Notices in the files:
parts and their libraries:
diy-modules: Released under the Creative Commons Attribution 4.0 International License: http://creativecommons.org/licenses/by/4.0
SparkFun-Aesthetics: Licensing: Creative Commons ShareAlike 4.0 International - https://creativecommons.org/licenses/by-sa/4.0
